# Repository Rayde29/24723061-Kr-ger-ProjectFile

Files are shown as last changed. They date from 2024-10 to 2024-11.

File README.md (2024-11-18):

# 24723061-Kruger-ProjectFile
Project File for Rayde Krüger-24723061- or Skripise Topic- Tip-thrust rotary wing aircraft
The file called Excel contains "Skripsie Budget" Which contains the budget and pin out for both boards used

Link to video:
https://1drv.ms/v/c/f0bb25edffddc46e/EVAi9ZLe4j9GsjdCYFR9vUkBoQ6bgEeh0lFj6d0QRGKrNw?e=6Zq3nG

Link to Code:
https://github.com/Rayde29/Skripsie_Code.git

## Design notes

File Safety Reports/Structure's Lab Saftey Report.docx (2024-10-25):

Mechatronics Lab Safety Report

Testing of a Tip-Thrust Rotary Aircraft

Date: | 23/09/2024
Student & SU nr: | Rayde Krüger 24723061
Student contact nr: | 063 694 9735
Supervisor: | Dr Andrew Gill
Lab engineer: | Mr Ferdi Zietsman
Head of safety: | Mr Cobus Zietsman

Emergency Contacts:

Contact: | Room nr. | Work nr. | Cell nr.
Mr F. Zietsman | 109 | - | 021 808 4954
Mr C. Zietsman | M212 | 021 808 4275 | -
Campus Security | - | 021 808 2333 | WhatsApp: 082 808 233
Fire Brigade | - | 021 808 8888 | -
Ambulance | - | 021 883 3444 | -

Signatures:

Student: (Rayde Krüger)
Supervisor: (Dr A. Gill)
Lab Engineer: (Mr CF. Zietsman)
Head of Safety: (C Zietsman)

Pressure vessels or pipes (check relevant box):

☒ No pressure vessels or pipes with pressure in excess of 50kPa are involved in this project.

☐ Pressure vessels or pipes in excess of 50kPa are involved – additional signature and report required (refer to Safety Report Guidelines on SUNLearn).

Hot work / working at heights / confined entry / excavation (check relevant box):

☒ No hot work / working heights / confined entry / excavation work involved in this project.

☐ Hot work / working heights / confined entry / excavation work (underline relevant work type(s)) involved in this project – additional signature and report required (refer to Safety Report Guidelines on SUNLearn).

Overview of Testing

Type of test and standard (if applicable):

Test type | Testing of tip-thrust rotary aircraft
Standard(s) | IEC 60950-1 / IEC 62368-1:

Equipment to be used:

Equipment type | Make & model | Measurement range (if applicable) | Resolution (if applicable)
40 A DC power supply | - | - | -
Oscilloscope | - | - | -
Soldering Iron | - | - | -
Load Cell 50KG | TAL220 Series | 0 to 50 kg | -
Load Cell Amplifier | HX711 | - | 24-bit

Detailed Experimental Procedure

The purpose of this section is to clearly communicate the purpose of equipment use and list the steps necessary to prepare the equipment for testing. This report will describe the testing of a tip-thrust rotary aircraft, and the risks associated with them. The purpose of the testing will be to determine the behaviour of the system’s rotor, the amount of thrust produced, and if directional thrust can be achieved.

Pitch control testing setup:

- Assemble the rotary wing aircraft
- Secure the rotary wing aircraft to the base
- Secure the rotor hub so it cannot rotate
- Ensure the correct voltage is being supplied by the power supply
- Connect the power supply to the hub
- Identify the emergency stop button (Power supply off switch)
- Ensure all the components have been correctly wired
- Ensure all wires, loose items or clothing are clear of the motors

Pitch control testing procedures:

- Switch on the power supply
- Ensure the hub is secure and there are no obstructions in its path in the event that it comes loose and rotates
- Calibrate the pitch sensor of the rotor
- Activate the tip-thrust motors on low-speed
- Slowly increase the thrust until the desired speed of the tip thrust motors, ensuring that the hub remains stationary
- Once the rotor is stable, set a target pitch for the PID controller to reach
- Change the target pitch multiple times to determine the response speed for the different pitch values.
- Record the results in an Excell spreadsheet
- Switch off the tip-thrust motors and repeat the experiment

Directional thrust testing setup:

- Assemble the rotary wing aircraft
- Secure the rotary wing aircraft to the base
- Ensure there are no obstructions in the rotor's path
- Ensure all components are securely attached to the aircraft
- Connect the load cells to the DAQ and ensure they are being received
- Calibrate the load cells using known weights
- Ensure the correct voltage is being supplied by the power supply
- Identify the emergency stop button (Power supply off switch)
- Ensure all the components have been correctly wired
- Connect the power supply to the hub
- Ensure all wires, loose items or clothing are clear of the motors

Directional thrust testing procedure:

- Switch on the power supply
- Calibrate the rotor pitch sensor
- Ensure that the rotor path is clear of any obstructions before switching on the tip-thrust motors on low-speed
- Set the target angular velocity of the rotor
- Wait until the angular velocity has become steady
- Record the response of the control system
- Record the data from the load cells
- Set directional flight mode
- Record the data from the load cells
- Repeat the experiment for different angular velocities and directions

Shut down procedure:

- Stop the software of the microcontroller and ensure all components are in a state to power down
- Turn off the power supply
- Wait until all components have stopped moving
- Remove the rotary wing aircraft from the base
- Disassemble components to fit into storage
- Remove the load cells
- Safely store components
- Clean up workstation

Warning Symbols

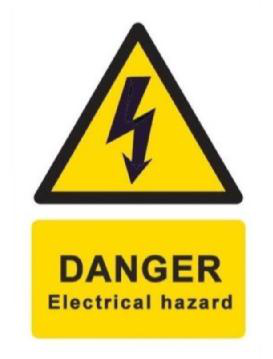
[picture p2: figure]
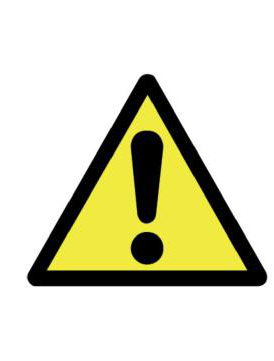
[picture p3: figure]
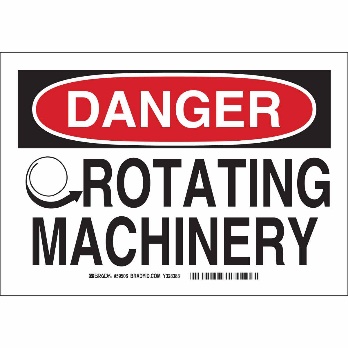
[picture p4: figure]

(a) Electrical hazard (b) General Warning (c) Rotating machinery warning

Figure 1: Applicable warning/hazard symbols

General Laboratory Safety

The following general laboratory safety instructions are applicable:

- No afterhours testing may be performed without the necessary permissions[^1].
- Full supervised training is required before testing may be undertaken. Permission to proceed with unsupervised testing should be signed off by the lab engineer.
- Closed shoes must be worn at all times.
- Emergency equipment must be located and easily accessible.
- Students may not work alone in the laboratory.
- Emergency exits must be known. The nearest exits applicable to the setup are provided in Appendix A of this document
- Loose clothing may not be worn. Loose hair must be tied up.
- Good housekeeping practices should be maintained during testing. The lab should be completely clean, including all equipment stored away, after testing. Refer to the General Housekeeping section for particulars regarding practices to be followed for this specific setup.
- No food or drink is permitted in the laboratory.
- Safety report must be visible and accessible during testing.
- No equipment or test may be left unattended.

Anticipated Interactions with Other Laboratory Users

Barriers between the rotary wing aircraft and other nearby projects to reduce the risk of components falling off and striking another student or their project.

General Housekeeping

- Keep workspace tidy while working
- Switch off power supplies after use
- Disassemble the rotor and place it in its storage
- Clean working surface, remove any debris and off cuttings
- Return all equipment to their storage
- Ensure the workstation is clear and clean
- Ensure no personal items are left behind

Fire Safety

The DC motors could potentially overheat. This can be avoided by ensuring the motors operate below the maximum operating voltage, ensuring that they do not overheat. Parts of the circuit could short and cause a fire. This hazard can be mitigated by using properly insulated wires and labelling the wires, so wires aren’t incorrectly connected and by having neat solders. In case of a fire, the evacuation plan can be seen in Appendix A. No earphones should be worn while working so fire alarms can be heard.

Activity Based Risk Assessment

Activity | Risk | Risk Type* (P/E) | Mitigating Steps | Classification of Risk Severity

GENERAL
Moving around the lab | Tripping or knocking over equipment | P | Be aware of the surrounding equipment and environment when walking in the lab | Acceptable risk
Power outages | Data loss and damage to equipment | E | Check the loadshedding schedule beforehand | Possible risk
Personal items | Theft of items | P | Don’t leave personal items unattended | Acceptable risk

TESTING PHASE
Installing electrical components | Electric shocks | P | Ensure the power is off when working with the components | Possible risk
| Shorting electrical components | E | Ensure all components are connected correctly before powering them | Acceptable risk
| Incorrect connections | E | Ensure components are connected according to the wiring diagram | Acceptable risk
Using hand tools | Injuries due to slippage | P | Ensure if a tool slips, no injuries can occur | Acceptable risk
Installing motors | Dropping motors | E | Handle motors with care | Acceptable risk
Assembling rotor | Pinching fingers | P | Ensure fingers are not caught in between components while assembling | Acceptable risk
Incorrect Calibration | Aircraft is uncontrollable | P/E | After calibrating the pitch, ensure the readings are correct | Acceptable risk
Loose wires or clothing caught in the motors | Getting items entangled by the motors | P/E | Don’t wear loose clothing and ensure any loose items are kept away from the motors | Acceptable risk
Rotor turning | Impact with the rotor | P/E | Ensure there are no obstructions with the rotors’ path | Possible risk
| Items detach from the rotor | P/E | Check that all items are securely attached to the rotor and hub | Possible risk
Rotor turning | Rotary aircraft tips over | P/E | Ensure the base is firmly secured | Possible risk
Load cell failure | Incorrect readings from the load cells | E | Calibrate the load cells before use | Acceptable risk
Testing motor | Motors overheat | E | Ensure the motors operate within the rated values | Acceptable risk
| Burns occur from motor overheating | P | Ensure the motors operate within the rated values | Acceptable risk
Testing software | Code not working as intended | P/E | Ensure the code is fully understood before it is uploaded | Acceptable risk
Backing up data | Data loss | E | Use a USB/ hard drive which is frequently updated. | Acceptable risk

*P – personal, E - equipment

Disciplinary Actions

Failure to comply with any of the aforementioned safety regulations or procedures will result in disciplinary action. Students will be issued an initial warning: after three warnings, the lab access is revoked for a month.

Appendix A: Emergency Evacuation Plans

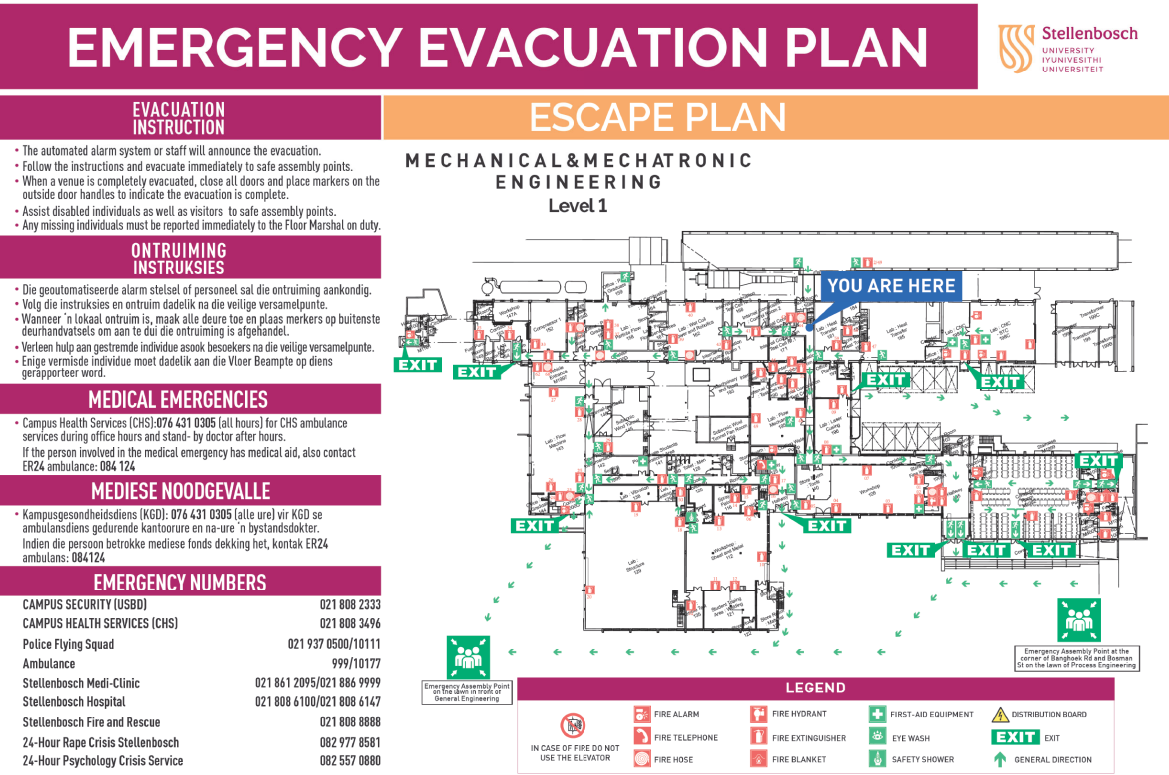
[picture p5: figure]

[^1] Written permission from supervisor and approved by the chief safety officer. Attach proof of this permission to this document and note here the times and conditions of the arrangement.

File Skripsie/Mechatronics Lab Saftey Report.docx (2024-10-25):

Mechatronics Lab Safety Report

Testing of Electronic Components and assembly of a Tip-Thrust Rotary Aircraft

Date: | 08/07/2024
Student & SU nr: | Rayde Krüger 24723061
Student contact nr: | 063 694 9735
Supervisor: | Dr Andrew Gill
Lab engineer: | Mr Kevin Neaves
Head of safety: | Mr Cobus Zietsman

Emergency Contacts:

Contact: | Room nr. | Work nr. | Cell nr.
Mr K. Neaves | 3001 | - | 021 808 4279
Mr C. Zietsman | M212 | 021 808 4275 | -
Campus Security | - | 021 808 2333 | WhatsApp: 082 808 233
Fire Brigade | - | 021 808 8888 | -
Ambulance | - | 021 883 3444 | -

Signatures:

Student: (Rayde Krüger)
Supervisor: (Dr A. Gill)
Lab Engineer: (Mr K. Neaves)
Head of Safety: (C Zietsman)

Pressure vessels or pipes (check relevant box):

☒ No pressure vessels or pipes with pressure in excess of 50kPa are involved in this project.

☐ Pressure vessels or pipes in excess of 50kPa are involved – additional signature and report required (refer to Safety Report Guidelines on SUNLearn).

Hot work / working at heights / confined entry / excavation (check relevant box):

☒ No hot work / working heights / confined entry / excavation work involved in this project.

☐ Hot work / working heights / confined entry / excavation work (underline relevant work type(s)) involved in this project – additional signature and report required (refer to Safety Report Guidelines on SUNLearn).

Overview of Testing

Type of test and standard (if applicable):

Test type | Testing electronic components and assembly of tip-thrust rotary aircraft
Standard(s) | IEC 60950-1 / IEC 62368-1:

Equipment to be used:

Equipment type | Make & model | Measurement range (if applicable) | Resolution (if applicable)
Power supply | - | - | -
Oscilloscope | - | - | -
Soldering Iron | - | - | -

Detailed Experimental Procedure

The purpose of this section is to clearly communicate the purpose of equipment use and list the steps necessary to prepare the equipment for testing. This report will describe the testing of the electronic components as well as the assembly of the tip-thrust rotary aircraft and the risks associated with them. The purpose of the testing will be to determine the behaviour of the electronics and to test the microcontroller’s programming to control these components. The tip-thrust aircraft will be assembled in the Mechatronics lab, but not tested and no propellers will be connected to the brushless motors during testing.

Electronics testing setup:

- Read through the electronic components datasheet and take note of the components' operating voltages
- Identify the emergency stop button (Power supply off switch)
- Ensure all wire connections are securely connected and no cables or components appear damaged.
- Label all wires to prevent incorrect connections
- Verify the power supply and the oscilloscope are functioning correctly

Testing procedure for electronics:

- Connect the electronic component being tested according to the wiring diagram
- Switch on the power supply and check the output voltage.
- Test the output signal from the microcontroller and the output of the electronic component being tested on the oscilloscope
- Run the microcontroller's program to be tested and observe how the components
- Change the program as needed and repeat

Assembly procedure for Tip-thrust Rotary Aircraft:

- Ensure all parts to be assembled are undamaged and function as intended.
- Assemble the parts as described by the CAD model.
- Install electronic components according to the design specifications
- Ensure all wiring is connected correctly and secured to prevent movement of the wiring.

Shut down procedure:

- Stop the software of the microcontroller and ensure all components are in a state to power down
- Turn off the power supply and oscilloscope
- Disassemble components to fit into storage
- Safely store components
- Clean up workstation

Warning Symbols


(a) Electrical hazard (b) General Warning

Figure 1: Applicable warning/hazard symbols

General Laboratory Safety

The following general laboratory safety instructions are applicable:

- No afterhours testing may be performed without the necessary permissions[^1].
- Full supervised training is required before testing may be undertaken. Permission to proceed with unsupervised testing should be signed off by the lab engineer.
- Closed shoes must be worn at all times.
- Emergency equipment must be located and easily accessible.
- Students may not work alone in the laboratory.
- Emergency exits must be known. The nearest exits applicable to the setup are provided in Appendix A of this document
- Loose clothing may not be worn. Loose hair must be tied up.
- Good housekeeping practices should be maintained during testing. The lab should be completely clean, including all equipment stored away, after testing. Refer to the General Housekeeping section for particulars regarding practices to be followed for this specific setup.
- No food or drink is permitted in the laboratory.
- Safety report must be visible and accessible during testing.
- No equipment or test may be left unattended.

Anticipated Interactions with other Laboratory Users

If possible, the student’s experimental setup will remain within the workspace with a space in between the nearest experiment.

General Housekeeping

- Keep workspace tidy while working
- Switch off power supplies after use
- Disassemble the rotor and place it in its storage
- Clean working surface, remove any debris and off cuttings
- Return all equipment to their storage
- Ensure the workstation is clear and clean
- Ensure no personal items are left behind

Fire Safety

The DC motors could potentially overheat. This can be avoided by ensuring the motors operate below the maximum operating voltage, ensuring that they do not overheat. Parts of the circuit could short and cause a fire. This hazard can be mitigated by using properly insulated wires and labelling the wires, so wires aren’t incorrectly connected and by having neat solders. In case of a fire, the evacuation plan can be seen in Appendix A. No earphones should be worn while working so fire alarms can be heard.

Activity Based Risk Assessment

Activity | Risk | Risk Type* (P/E) | Mitigating Steps | Classification of Risk Severity

GENERAL
Moving around the lab | Tripping or knocking over equipment | P | Be aware of the surrounding equipment and environment when walking in the lab | Acceptable risk
Power outages | Data loss and damage to equipment | E | Check the loadshedding schedule beforehand | Possible risk
Personal items | Theft of items | P | Don’t leave personal items unattended | Acceptable risk

ASSEMBLY PHASE
Soldering components | Burns from equipment and solder | P | Handle the equipment carefully | Acceptable risk
| Damage components | E | Ensure the soldering iron is not placed where it could damage the component | Acceptable risk
Installing electrical components | Electric shocks | P | Ensure the power is off when working with the components | Acceptable risk
| Shorting electrical components | E | Ensure all components are connected correctly before powering them | Acceptable risk
| Incorrect connections | E | Ensure components are connected according to the wiring diagram | Acceptable risk
Using hand tools | Injuries due to slippage | P | Ensure if a tool slips, no injuries can occur | Acceptable risk
Installing motors | Dropping motors | E | Handle motors with care | Acceptable risk
Assembling rotor | Pinching fingers | P | Ensure fingers are not caught in between components while assembling | Acceptable risk
| Cuts from burrs | P | Clean the edges of cut components | Acceptable risk

TESTING PHASE
Testing motor | Motors overheat | E | Ensure the motors operate within the rated values | Acceptable risk
| Burns occur from motor overheating | P | Ensure the motors operate within the rated values | Acceptable risk
Testing software | Code not working as intended | P/E | Ensure the code is fully understood before it is uploaded | Acceptable risk
Backing up data | Data loss | E | Use a USB/ hard drive which is frequently updated. | Acceptable risk

*P – personal, E - equipment

Disciplinary Actions

Failure to comply with any of the aforementioned safety regulations or procedures will result in disciplinary action. Students will be issued an initial warning: after three warnings, the lab access is revoked for a month.

Appendix A: Emergency Evacuation Plans

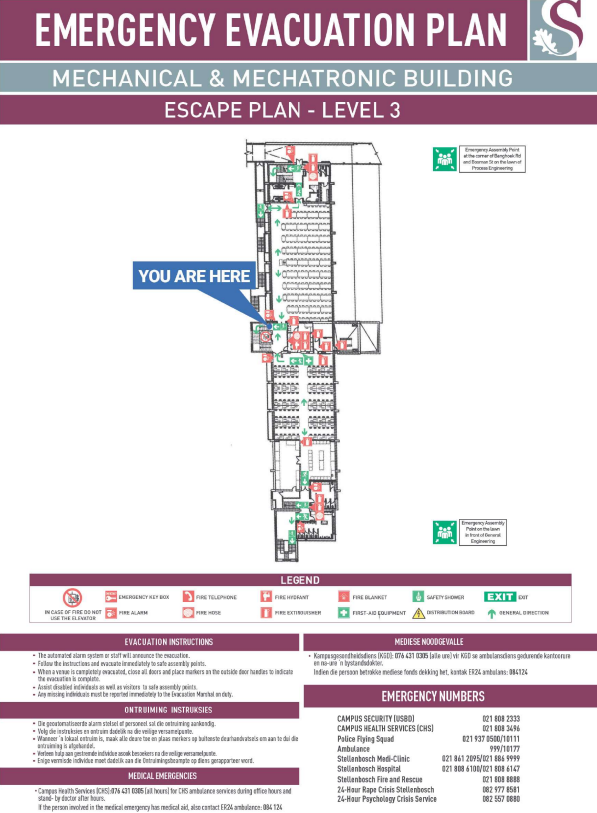
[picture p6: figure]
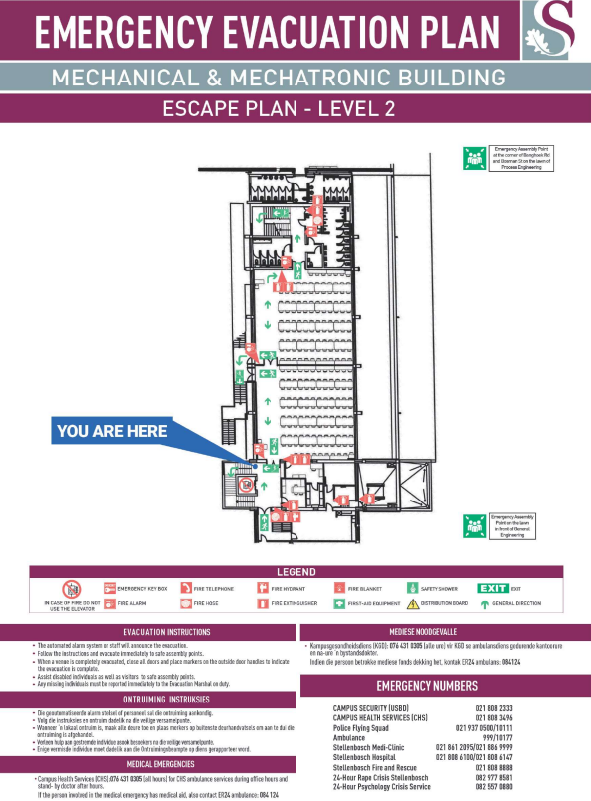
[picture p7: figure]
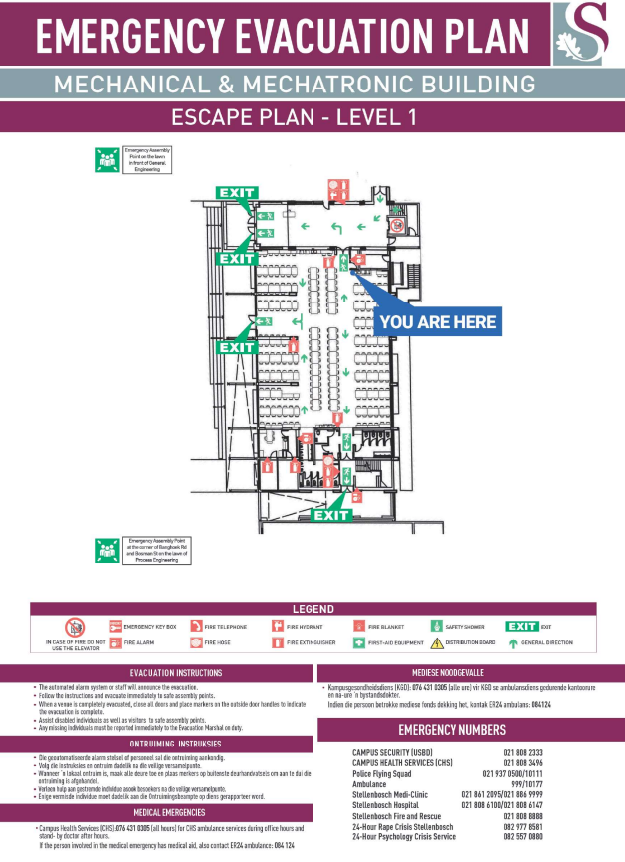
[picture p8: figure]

[^1] Written permission from supervisor and approved by the chief safety officer. Attach proof of this permission to this document and note here the times and conditions of the arrangement.

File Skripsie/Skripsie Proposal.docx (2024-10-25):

# Skripsie proposal: Tip-propelled rotary-wing aircraft

## Goal:

The goal of this project will be to design and build a rotary-wing aircraft which actuates its blades through the use of propulsion situated at the tip of the blades. The variation in propulsion should control translation in both the vertical and horizontal plane (the lift and rotor blade pitch). The aircraft should demonstrate that it is controllable and can sustain flight while being stable.

## Tentative Questions

### Can the rotary-wing aircraft be fully controlled using just the tip propulsion?

Investigate to determine if the direction of the aircraft be can controlled by adjusting the thrust generated from the tip propulsion or are external actuators and mechanisms, such as a swashplate, are required.

## Background

Traditional methods for actuating the blades consist of using a turboshaft engine to drive the rotor shaft, which rotates the blades. According to Newton's third law, the motor causes a torque on the fuselage from where the engine bevel gear connects to the rotor bevel gear and thus a tail rotor is required to compensate for this force. The tail rotor is mechanically linked to the main rotor so its rotational speed cannot change, instead to increase are decrease its force, the pitch of the blades is adjusted. Similarly, to move the helicopter in a certain direction the pitch of the blades at certain positions is adjusted using a swashplate, which would cause an increase in the pitch at one point and a decrease at the opposite point. This would create increased lift from the blade with the higher pitch and conversely, the decreased pitch would reduce lift. This creates a force upward force and a downward force located opposite to the upward force creating a moment about the fuselage. As seen with gyroscopic procession, this causes the force to act perpendicular to the applied force. Moving the helicopter in the direction of the force.

Traditional helicopters rely on the tail rotor to maintain control, if it malfunctions, it will cause the helicopter to become uncontrollable. The proposed idea to use tip propulsion to produce rotation has the benefit of eliminating the toque felt by the fuselage and thus eliminating the need for a tail rotor, with the added benefit of it being cheaper, lighter and reducing the need for high gearboxes and clutches. (Nenad Kolarević, 2020)

Research has shown most propulsion-tipped rotary aircraft make use of small jet engines placed at the tips of the blade. This was witnessed in the design of the Fairey Rotodyne. While the Rotodyne was a gyrodyne, meaning it made use of freely rotating rotor blades to produce lift, it had jet-tipped blades to allow for hovering and vertical take-off and landing. While this was intended to revolutionise air travel, the jet tips proved to be too loud for its intended purpose of inter-city travel (Mustard, 2019). Another option, which proved to be effective is demonstrated in the French helicopter the SO 1221S Djin, which made use of compressed air from a turbine-driven air compressor. (Heli archive, 2023).

As seen, this concept has been explored and has some benefits, yet is still fairly rare. Some of the disadvantages of this type of articulation are transmitting power to the rotating tips, increased noise, and the fact that there is added weight cantilevered at the end of the blade tips. These are a few of the challenges that need to be considered when creating the design for a propulsion-tipped rotary aircraft.

## Project Synopsis

### Propulsion

The first step required is a decision on the type of propulsion. These include jet engines, compressed air or by using electrical motors. It is believed that even at this time the possibility of jet engines can be ruled out for various reasons, leaving compressed air and electrical motors. Using the motors, a battery could be used to store potential energy, whereas a tank would be needed for compressed air. Controlling the speed can easily be done by increasing and decreasing the voltage to the electric motors, whereas for the compressed air, the output nozzle would need to increase and decrease in diameter, potentially with an iris mechanism and a servo motor. Lastly, the stored energy needs to be transmitted through the rotating blades, this can be achieved through a slip ring for the electric motors or using a swivel connector for the compressed air.

The only advantage of using the compressed air over the electric motors is that there wouldn’t need to be anything mounted at the tip of the wings, as it can be transmitted through tubing to the tips. While more research should be done into the matter, the electric motors have more precise control, most likely have a longer flight time and are less complicated. There is a high likelihood that this will be the chosen option moving forward.

### Designing and Controllability

Experiments need to be done to determine a method to adjust the pitch of the blade. Possible methods include the traditional use of a swashplate, actuators on each blade or by making a mechanism for which varying the individual speed of the tip propulsions adjusts the pitch. No CFD will be expected to be done.

Once the pitching mechanism has been decided on, the first prototype can be designed and created. This prototype will make use of a microcontroller and various sensors to ensure the aircraft can be controlled. A control system for this system will have to be made for this to make it possible to control the motion. Due to the complex nature and the desired control of this model, a state space controller would be the best choice, however, it may be difficult to derive an accurate model for the system and thus a PID controller might need to be used instead. The prototype will take in human input and not be autonomous.

### Testing

Once a control system has been implemented the prototype can be tested by securing it to four load cells (presumably in an ‘X’ configuration). From the load cells, it will be seen if thrust can be created such that the aircraft will go in the direction that has been instructed of it, thereby demonstrating the controllability of the prototype.

## Final remarks

The above illustrates the basic procedure that will be followed when designing and building the tip-propelled rotary-wing aircraft. Whilst care has been taken, it is anticipated that additional problems will be encountered during the course of this work, the overcoming of which will be an exciting challenge.

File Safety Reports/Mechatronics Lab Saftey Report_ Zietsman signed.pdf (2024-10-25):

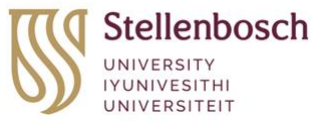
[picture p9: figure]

# Mechatronics Lab Safety Report

### Testing of Electronic Components and assembly of a Tip-Thrust Rotary Aircraft

Date: | 08/07/2024
Student & SU nr: | Rayde Krüger 24723061
Student contact nr: | 063 694 9735
Supervisor: | Dr Andrew Gill
Lab engineer: | Mr Kevin Neaves
Head of safety: | Mr Cobus Zietsman

Emergency Contacts:

Contact: | Room nr. | Work nr. | Cell nr.
Mr K. Neaves | 3001 | - | 021 808 4279
Mr C. Zietsman | M212 | 021 808 4275 | -
Campus Security | - | 021 808 2333 | WhatsApp: 082 808 233
Fire Brigade | - | 021 808 8888 | -
Ambulance | - | 021 883 3444 | -

Signatures:

Student: (Rayde Krüger) | motors.

Supervisor: (Dr A. Gill)

Lab Engineer: (Mr K. Neaves) | 12/8/2024

Head of Safety: (C Zietsman)

Pressure vessels or pipes (check relevant box):
☒ | No pressure vessels or pipes with pressure in excess of 50kPa are involved in this project.
☐ | Pressure vessels or pipes in excess of 50kPa are involved – additional signature and report
required (refer to Safety Report Guidelines on SUNLearn).

Hot work / working at heights / confined entry / excavation (check relevant box):
☒ | No hot work / working heights / confined entry / excavation work involved in this project.
☐ | Hot work / working heights / confined entry / excavation work (underline relevant work
type(s)) involved in this project – additional signature and report required (refer to Safety Report Guidelines on SUNLearn).

## Ensure no wires, loose items of clothing hair etc. is clear of the

### Overview of Testing

Type of test and standard (if applicable):

Test type | Testing electronic components and assembly of tip-thrust rotary aircraft
Standard(s) | IEC 60950-1 / IEC 62368-1:

Equipment to be used:

Equipment type | Make & model | Measurement range (if applicable) | Resolution (if applicable)
Power supply | - | - | -
Oscilloscope | - | - | -
Soldering Iron | - | - | -

### Detailed Experimental Procedure

The purpose of this section is to clearly communicate the purpose of equipment use and list the steps necessary to prepare the equipment for testing. This report will describe the testing of the electronic components as well as the assembly of the tip-thrust rotary aircraft and the risks associated with them. The purpose of the testing will be to determine the behaviour of the electronics and to test the microcontroller’s programming to control these components. The tip-thrust aircraft will be assembled in the Mechatronics lab, but not tested and no propellers will be connected to the brushless motors during testing.
Electronics testing setup:
- Read through the electronic components datasheet and take note of the components' operating voltages
- Identify the emergency stop button (Power supply off switch)
- Ensure all wire connections are securely connected and no cables or components appear damaged.
- Label all wires to prevent incorrect connections
- Verify the power supply and the oscilloscope are functioning correctly
Testing procedure for electronics:
- Connect the electronic component being tested according to the wiring diagram
- Switch on the power supply and check the output voltage.
- Test the output signal from the microcontroller and the output of the electronic component being tested on the oscilloscope
- Run the microcontroller's program to be tested and observe how the components
- Change the program as needed and repeat

Assembly procedure for Tip-thrust Rotary Aircraft:

- Ensure all parts to be assembled are undamaged and function as intended.
- Assemble the parts as described by the CAD model.
- Install electronic components according to the design specifications
- Ensure all wiring is connected correctly and secured to prevent movement of the wiring.

Shut down procedure:

- Stop the software of the microcontroller and ensure all components are in a state to power down
- Turn off the power supply and oscilloscope
- Disassemble components to fit into storage
- Safely store components
- Clean up workstation

### Warning Symbols

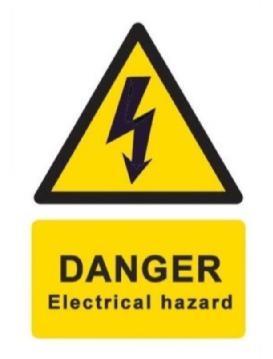
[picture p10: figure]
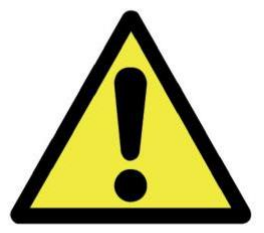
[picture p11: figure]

(a) Electrical hazard | (b) General Warning

Figure 1: Applicable warning/hazard symbols

### General Laboratory Safety

The following general laboratory safety instructions are applicable:

- No afterhours testing may be performed without the necessary permissions¹
- Full supervised training is required before testing may be undertaken. Permission to proceed with unsupervised testing should be signed off by the lab engineer.
- Closed shoes must be worn at all times.
- Emergency equipment must be located and easily accessible.
- Students may not work alone in the laboratory.
- Emergency exits must be known. The nearest exits applicable to the setup are provided in Appendix A of this document
- Loose clothing may not be worn. Loose hair must be tied up.
- Good housekeeping practices should be maintained during testing. The lab should be completely clean, including all equipment stored away, after testing. Refer to the General Housekeeping section for particulars regarding practices to be followed for this specific setup.
- No food or drink is permitted in the laboratory.

1 Written permission from supervisor and approved by the chief safety officer. Attach proof of this permission to this document and note here the times and conditions of the arrangement.

- Safety report must be visible and accessible during testing.
- No equipment or test may be left unattended.

### Anticipated Interactions with other Laboratory Users

If possible, the student’s experimental setup will remain within the workspace with a space in between the nearest experiment.

### General Housekeeping

- Keep workspace tidy while working
- Switch off power supplies after use
- Disassemble the rotor and place it in its storage
- Clean working surface, remove any debris and off cuttings
- Return all equipment to their storage
- Ensure the workstation is clear and clean
- Ensure no personal items are left behind

### Fire Safety

The DC motors could potentially overheat. This can be avoided by ensuring the motors operate below the maximum operating voltage, ensuring that they do not overheat. Parts of the circuit could short and cause a fire. This hazard can be mitigated by using properly insulated wires and labelling the wires, so wires aren’t incorrectly connected and by having neat solders. In case of a fire, the evacuation plan can be seen in Appendix A. No earphones should be worn while working so fire alarms can be heard.

### Activity Based Risk Assessment

Activity | Risk | Risk Type* (P/E)
Mitigating Steps | Classification of Risk
Severity

GENERAL
Moving around the lab | Tripping or knocking over equipment | P | Be aware of the surrounding equipment and environment when walking in the lab | Acceptable risk
Power outages | Data loss and damage to equipment | E | Check the loadshedding schedule beforehand | Possible risk
Personal items | Theft of items | P | Don’t leave personal items unattended | Acceptable risk

ASSEMBLY PHASE
Soldering components | Burns from equipment and solder | P | Handle the equipment carefully | Acceptable risk
| Damage components | E | Ensure the soldering iron is not placed where it | Acceptable risk

| | | could damage the component
Installing electrical components | Electric shocks | P | Ensure the power is off when working with the components | Acceptable risk
| Shorting electrical components | E | Ensure all components are connected correctly before powering them | Acceptable risk
| Incorrect connections | E | Ensure components are connected according to the wiring diagram | Acceptable risk
Using hand tools | Injuries due to slippage | P | Ensure if a tool slips, no injuries can occur | Acceptable risk
Installing motors | Dropping motors | E | Handle motors with care | Acceptable risk
Assembling rotor | Pinching fingers | P | Ensure fingers are not caught in between components while assembling | Acceptable risk
| Cuts from burrs | P | Clean the edges of cut components | Acceptable risk

TESTING PHASE
Testing motor | Motors overheat | E | Ensure the motors operate within the rated values | Acceptable risk
| Burns occur from motor overheating | P | Ensure the motors operate within the rated values | Acceptable risk
Testing software | Code not working as intended | P/E | Ensure the code is fully understood before it is uploaded | Acceptable risk
Backing up data | Data loss | E | Use a USB/ hard drive which is frequently updated. | Acceptable risk

*P – personal, E - equipment

### Disciplinary Actions

Failure to comply with any of the aforementioned safety regulations or procedures will result in disciplinary action. Students will be issued an initial warning: after three warnings, the lab access is revoked for a month.

### Appendix A: Emergency Evacuation Plans

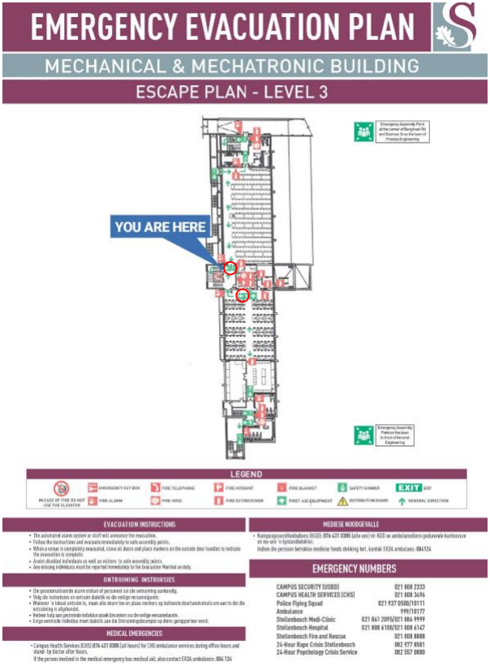
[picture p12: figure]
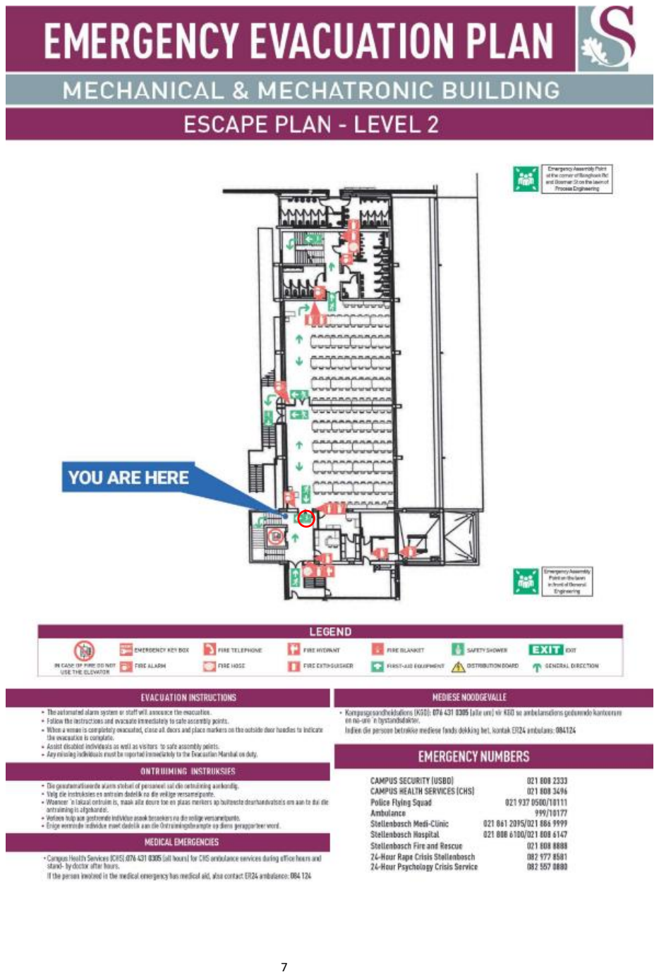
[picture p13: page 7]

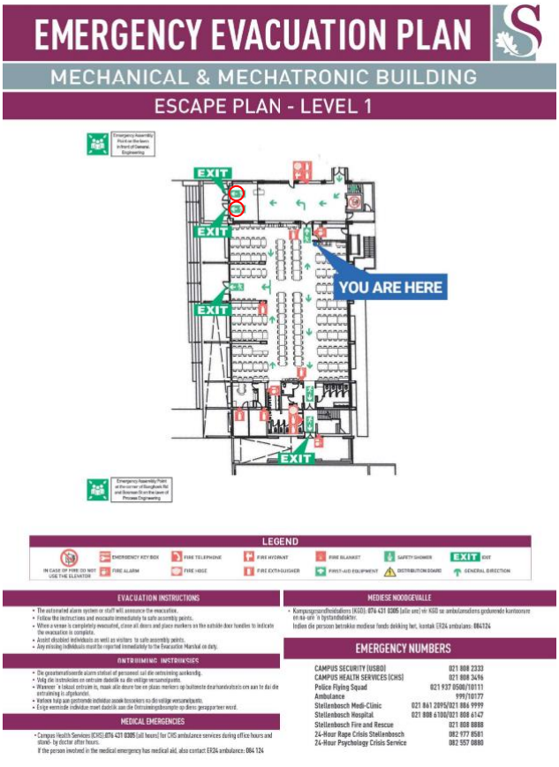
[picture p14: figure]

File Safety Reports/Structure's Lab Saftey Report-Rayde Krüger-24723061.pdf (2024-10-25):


# Mechatronics Lab Safety Report

### Testing of a Tip-Thrust Rotary Aircraft

Date: | 23/09/2024
Student & SU nr: | Rayde Krüger 24723061
Student contact nr: | 063 694 9735
Supervisor: | Dr Andrew Gill
Lab engineer: | Mr Ferdi Zietsman
Head of safety: | Mr Cobus Zietsman

Emergency Contacts:

Contact: | Room nr. | Work nr. | Cell nr.
Mr CF. Zietsman | 109 | - | 021 808 4954
Mr C. Zietsman | M212 | 021 808 4275 | -
Campus Security | - | 021 808 2333 | WhatsApp: 082 808 233
Fire Brigade | - | 021 808 8888 | -
Ambulance | - | 021 883 3444 | -

Signatures:

Student: (Rayde Krüger)

Supervisor: (Dr A. Gill)

Lab Engineer: (Mr CF. Zietsman)

Head of Safety: (C Zietsman)

Pressure vessels or pipes (check relevant box):
☒ | No pressure vessels or pipes with pressure in excess of 50kPa are involved in this project.
☐ | Pressure vessels or pipes in excess of 50kPa are involved – additional signature and report
required (refer to Safety Report Guidelines on SUNLearn).

Hot work / working at heights / confined entry / excavation (check relevant box):
☒ | No hot work / working heights / confined entry / excavation work involved in this project.
☐ | Hot work / working heights / confined entry / excavation work (underline relevant work
type(s)) involved in this project – additional signature and report required (refer to Safety Report Guidelines on SUNLearn).

### Overview of Testing

Type of test and standard (if applicable):

Test type | Testing of tip-thrust rotary aircraft
Standard(s) | IEC 60950-1 / IEC 62368-1:

Equipment to be used:

Equipment type | Make & model | Measurement range (if applicable) | Resolution (if applicable)
40 A DC power supply | - | - -
Oscilloscope | - | - | -
Soldering Iron | - | - | -
Load Cell 50KG | TAL220 Series | 0 to 50 kg | -
Load Cell Amplifier | HX711 | - | 24-bit

### Detailed Experimental Procedure

The purpose of this section is to clearly communicate the purpose of equipment use and list the steps necessary to prepare the equipment for testing. This report will describe the testing of a tip-thrust rotary aircraft, and the risks associated with them. The purpose of the testing will be to determine the behaviour of the system’s rotor, the amount of thrust produced, and if directional thrust can be achieved.

Pitch control testing setup:
- Assemble the rotary wing aircraft
- Secure the rotary wing aircraft to the base
- Secure the rotor hub so it cannot rotate
- Ensure the correct voltage is being supplied by the power supply
- Connect the power supply to the hub
- Identify the emergency stop button (Power supply off switch)
- Ensure all the components have been correctly wired
- Ensure all wires, loose items or clothing are clear of the motors

Pitch control testing procedures:
- Switch on the power supply
- Ensure the hub is secure and there are no obstructions in its path in the event that it comes loose and rotates
- Calibrate the pitch sensor of the rotor
- Activate the tip-thrust motors on low-speed
- Slowly increase the thrust until the desired speed of the tip thrust motors, ensuring that the hub remains stationary
- Once the rotor is stable, set a target pitch for the PID controller to reach
- Change the target pitch multiple times to determine the response speed for the different pitch values.
- Record the results in an Excell spreadsheet
- Switch off the tip-thrust motors and repeat the experiment

Directional thrust testing setup:
- Assemble the rotary wing aircraft
- Secure the rotary wing aircraft to the base
- Ensure there are no obstructions in the rotor's path
- Ensure all components are securely attached to the aircraft
- Connect the load cells to the DAQ and ensure they are being received
- Calibrate the load cells using known weights
- Ensure the correct voltage is being supplied by the power supply
- Identify the emergency stop button (Power supply off switch)
- Ensure all the components have been correctly wired
- Connect the power supply to the hub
- Ensure all wires, loose items or clothing are clear of the motors

Directional thrust testing procedure:
- Switch on the power supply
- Calibrate the rotor pitch sensor
- Ensure that the rotor path is clear of any obstructions before switching on the tip-thrust motors on low-speed
- Set the target angular velocity of the rotor
- Wait until the angular velocity has become steady
- Record the response of the control system
- Record the data from the load cells
- Set directional flight mode
- Record the data from the load cells
- Repeat the experiment for different angular velocities and directions

Shut down procedure:

- Stop the software of the microcontroller and ensure all components are in a state to power down
- Turn off the power supply
- Wait until all components have stopped moving
- Remove the rotary wing aircraft from the base
- Disassemble components to fit into storage
- Remove the load cells
- Safely store components
- Clean up workstation

### Warning Symbols

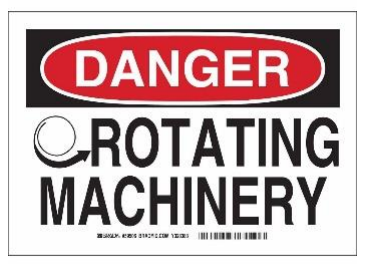
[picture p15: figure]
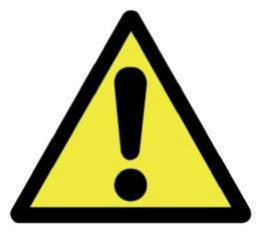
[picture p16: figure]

(a) Electrical hazard | (b) General Warning | (c) Rotating machinery warning

Figure 1: Applicable warning/hazard symbols

### General Laboratory Safety

The following general laboratory safety instructions are applicable:

- No afterhours testing may be performed without the necessary permissions¹
- Full supervised training is required before testing may be undertaken. Permission to proceed with unsupervised testing should be signed off by the lab engineer.
- Closed shoes must be worn at all times.
- Emergency equipment must be located and easily accessible.
- Students may not work alone in the laboratory.
- Emergency exits must be known. The nearest exits applicable to the setup are provided in Appendix A of this document
- Loose clothing may not be worn. Loose hair must be tied up.
- Good housekeeping practices should be maintained during testing. The lab should be completely clean, including all equipment stored away, after testing. Refer to the General Housekeeping section for particulars regarding practices to be followed for this specific setup.
- No food or drink is permitted in the laboratory.
- Safety report must be visible and accessible during testing.
- No equipment or test may be left unattended.

### Anticipated Interactions with Other Laboratory Users

Barriers between the rotary wing aircraft and other nearby projects to reduce the risk of components falling off and striking another student or their project.

### General Housekeeping

- Keep workspace tidy while working
- Switch off power supplies after use
- Disassemble the rotor and place it in its storage
- Clean working surface, remove any debris and off cuttings
- Return all equipment to their storage
- Ensure the workstation is clear and clean
- Ensure no personal items are left behind

### Fire Safety

1 Written permission from supervisor and approved by the chief safety officer. Attach proof of this permission to this document and note here the times and conditions of the arrangement.

The DC motors could potentially overheat. This can be avoided by ensuring the motors operate below the maximum operating voltage, ensuring that they do not overheat. Parts of the circuit could short and cause a fire. This hazard can be mitigated by using properly insulated wires and labelling the wires, so wires aren’t incorrectly connected and by having neat solders. In case of a fire, the evacuation plan can be seen in Appendix A. No earphones should be worn while working so fire alarms can be heard.

### Activity Based Risk Assessment

Activity | Risk | Risk Type* (P/E)
Mitigating Steps | Classification of Risk
Severity

GENERAL
Moving around the lab | Tripping or knocking over equipment | P | Be aware of the surrounding equipment and environment when walking in the lab | Acceptable risk
Power outages | Data loss and damage to equipment | E | Check the loadshedding schedule beforehand | Possible risk
Personal items | Theft of items | P | Don’t leave personal items unattended | Acceptable risk

TESTING PHASE
Installing electrical components | Electric shocks | P | Ensure the power is off when working with the components | Possible risk
| Shorting electrical components | E | Ensure all components are connected correctly before powering them | Acceptable risk
| Incorrect connections | E | Ensure components are connected according to the wiring diagram | Acceptable risk
Using hand tools | Injuries due to slippage | P | Ensure if a tool slips, no injuries can occur | Acceptable risk
Installing motors | Dropping motors | E | Handle motors with care | Acceptable risk
Assembling rotor | Pinching fingers | P | Ensure fingers are not caught in between components while assembling | Acceptable risk
Incorrect Calibration | Aircraft is uncontrollable | P/E | After calibrating the pitch, ensure the readings are correct | Acceptable risk
Loose wires or clothing caught in the motors | Getting items entangled by the motors | P/E | Don’t wear loose clothing and ensure any loose items are kept away from the motors | Acceptable risk
Rotor turning | Impact with the rotor | P/E | Ensure there are no obstructions with the rotors’ path | Possible risk
| Items detach from the rotor | P/E | Check that all items are securely attached to the rotor and hub | Possible risk

Rotor turning | Rotary aircraft tips over | P/E | Ensure the base is firmly secured | Possible risk
Load cell failure | Incorrect readings from the load cells | E | Calibrate the load cells before use | Acceptable risk
Testing motor | Motors overheat | E | Ensure the motors operate within the rated values | Acceptable risk
| Burns occur from motor overheating | P | Ensure the motors operate within the rated values | Acceptable risk
Testing software | Code not working as intended | P/E | Ensure the code is fully understood before it is uploaded | Acceptable risk
Backing up data | Data loss | E | Use a USB/ hard drive which is frequently updated. | Acceptable risk

*P – personal, E - equipment

### Disciplinary Actions

Failure to comply with any of the aforementioned safety regulations or procedures will result in disciplinary action. Students will be issued an initial warning: after three warnings, the lab access is revoked for a month.

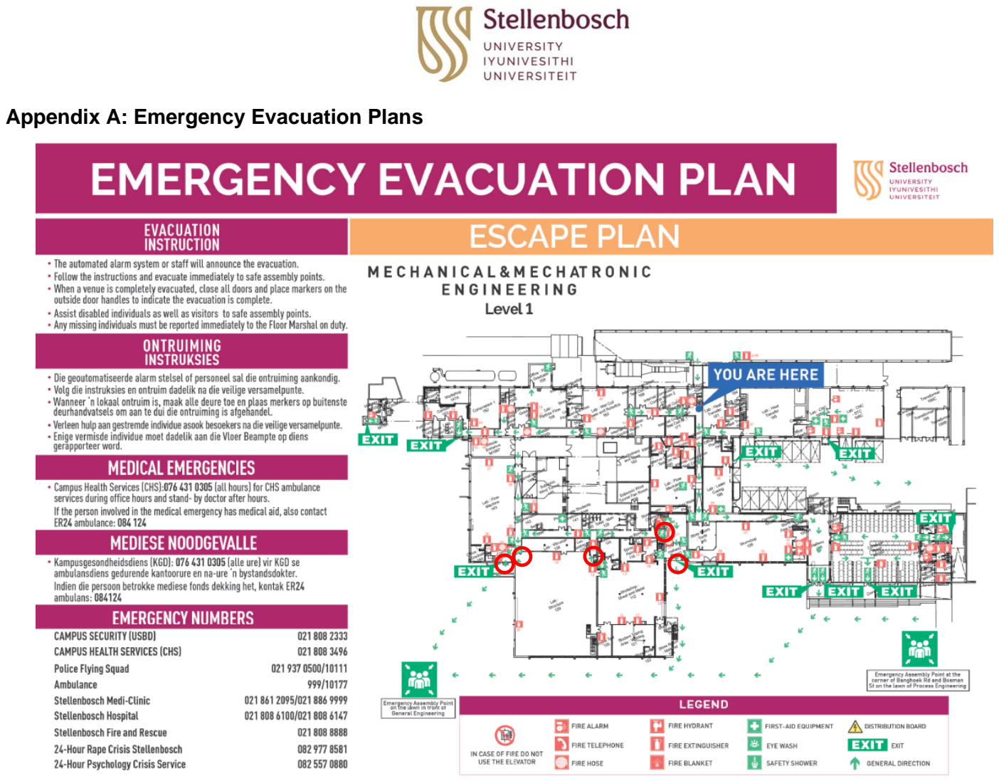
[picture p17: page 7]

### Appendix A: Emergency Evacuation Plans

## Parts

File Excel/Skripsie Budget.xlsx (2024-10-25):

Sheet: Full Budget
Item | Supplier | Price per unit | Quantity | Unit | Shipping | Category | Status | Total | Website | a
HKD NRF24L01+ TRANSCEIVER MODULE | Communica | R 29.00 | 2 | items | R 99.87 | Electronics | Received | R 157.88 |  |  | Not ordered
30a Electronic Speed Control Brushless | Takealot | R 230.00 | 4 | items | R 0.00 | Electroncis | Received | R 920.00 |  | s | Quote sent
Flash 1303.5 5500kv Brushless Motor | FPV Fanatics | R 285.00 | 4 | items | R 80.00 | Electroncis | Received | R 1220.00 |  | s | Ordered | 757
LOCK NUT 20X32X6MM M20X1.0 THREAD BTC | BMG | R 24.92 | 1 | items | R 80.00 | Mechanical | Received | R 104.92 | https://bmgworld.net/bmg/en/ZAR/All-Categories/Bearings/Accessories/Lock-Nuts/KM-04/p/KM%2004 | s | Received
BM0805FB-ISB (Bushing) | Bearings Online SA | R 23.00 | 4 | items | R 80.00 | Mechanical | Received | R 172.00 | https://bearingsonlinesa.co.za/shop/bm-0805-fb-8-x-10-x-5-isb/ | s
51104-ISB Thrust bearing | Bearings Online SA | R 95.00 | 2 | items | R 0.00 | Mechanical | Received | R 190.00 | https://bearingsonlinesa.co.za/shop/51104-20-x-35-x-10-isb/ | s
HQ Durable Prop 2.9X2.9X4 Grey | Flying Robot | R 45.00 | 1 | set | R 80.00 | Mechanical | Received | R 125.00 | https://flyingrobot.co/products/hq-durable-prop-2-9x2-9x4-grey-2cw-2ccw-poly-carbonate | s
 |  |  |  |  |  |  | Received
Hall effect | Micro Robotics | R 13.80 | 1 | packet (4) | R 0.00 | Electronics | Received | R 13.80 |  | s
Power Supply | Takealot | R 349.00 | 1 | items | R 0.00 | Electronics | Received | R 349.00
Slip Ring 4 Wire 20A Diameter 22mm | Micro Robotics | R 752.00 | 1 | items | R 0.00 | Electronics | Received | R 752.00
Magnets | Takealot | R 170.00 | 1 |  | R 0.00 | Mechanical | Received | R 170.00 |  | s
Black Bill | Micro Robotics | R 110.00 | 1 |  |  | Electronics | Received | R 110.00 |  | s
LEDS | Micro Robotics | R 25.00 | 1 | PACKET (25) |  | Electronics | Received | R 25.00
Wiring | Micro Robotics | R 33.00 | 2 | m | R 0.00 | Electronics | Received | R 66.00
Batterty Connectors | Micro Robotics | R 51.00 | 2 | items | R 0.00 | Electronics | Received | R 102.00
Regulators | Micro Robotics | R 19.00 | 1 | Packet | R 0.00 | Electronics | Received | R 19.00
3 pin connectors | Micro Robotics | R 34.00 | 4 | items | R 0.00 | Electronics | Received | R 136.00
 |  |  |  |  |  |  | Received | R 0.00
3D Printing |  | R 757.00 | 1 | 3D Prints | R 0.00 | Mechanical | Received | R 757.00 |  | s
Workshop |  | R 10.00 | 1 | Parts | R 0.00 | Mechanical | Received | R 10.00 |  | s
 |  |  |  |  |  |  | Received | R 0.00 |  | s
Total: |  |  |  |  | R 179.87 |  |  | R 5399.60
Predicted total: |  |  |  |  |  |  |  | R 5399.60

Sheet: Pin Out
Port | Pin | I/O Function | USART | ADC | PWM | SPI | TIM | FSMC | Other | Avliable | Function
PA | 0 | Digital I/O | None | ADC1_IN0 | None | None | TIM2_CH1_ETR | None | WKUP, RTC_TAMP1 | No | Rotor Pitch 1 | 12 V
PA | 1 | Digital I/O | None | ADC1_IN1 | None | None | TIM2_CH2, TIM5_CH2 | None | WKUP2, RTC_TAMP2 | No | Rotor Pitch 2 | 5 V
PA | 2 | Digital I/O | USART2_TX | ADC1_IN2 | TIM2_CH3 | None | TIM5_CH3 | None | ETH_MDIO | Yes |  | 3.3V
PA | 3 | Digital I/O | USART2_RX | ADC1_IN3 | TIM2_CH4 | None | TIM5_CH4 | None | ETH_MII_COL | No | SPI 1 Chip Enable | Data
PA | 4 | Digital I/O | None | ADC1_IN4 | None | SPI1_NSS | TIM5_CH1 | None | DAC_OUT1 | No | SP1 Chip Select 2 | Input/Output
PA | 5 | Digital I/O | None | ADC1_IN5 | None | SPI1_SCK | TIM5_CH2 | None | DAC_OUT2 | No | SPI 1 SCK | analogue/sensors
PA | 6 | Digital I/O | None | ADC1_IN6 | TIM3_CH1 | SPI1_MISO | TIM13_CH1 | None | ETH_MII_RX_CLK | No | SPI 1 MISO
PA | 7 | Digital I/O | None | ADC1_IN7 | TIM3_CH2 | SPI1_MOSI | TIM14_CH1 | None | ETH_MII_RX_DV | No | SPI 1 MOSI
PA | 8 | Digital I/O | None | None | TIM1_CH1 | None | TIM1_CH1N | None | MCO1 | Yes
PA | 9 | Digital I/O | USART1_TX | None | TIM1_CH2 | None | TIM1_CH2N | None | None | Yes
PA | 10 | Digital I/O | USART1_RX | None | TIM1_CH3 | None | TIM1_CH3N | None | None | Yes
PA | 11 | Digital I/O | USART1_CTS | None | None | None | TIM1_CH4 | None | OTG_FS_DM | Yes
PA | 12 | Digital I/O | USART1_RTS | None | None | None | TIM1_ETR | None | OTG_FS_DP | Yes
PA | 13 | Digital I/O | None | None | None | None | None | None | SWDIO | Yes
PA | 14 | Digital I/O | None | None | None | None | None | None | SWCLK | Yes
PA | 15 | Digital I/O | USART3_TX | None | None | SPI3_NSS | TIM2_CH1_ETR | None | JTDI | Yes
PB | 0 | Digital I/O | None | ADC1_IN8 | TIM3_CH3 | None | TIM8_CH2N | None | None | No | Tim3_ch 3 - PWM- Top Motor, Rotor 2
PB | 1 | Digital I/O | None | ADC1_IN9 | TIM3_CH4 | None | TIM8_CH3N | None | None | No | Tim3_ch 4 - PWM- Bottom Motor, Rotor 2
PB | 2 | Digital I/O | None | None | None | None | TIM2_CH4, TIM4_CH1 | None | Boot1 | Yes
PB | 3 | Digital I/O | USART2_CK | None | None | SPI1_SCK | TIM2_CH2, TIM5_CH2 | None | JTDO/TRACESWO | No | Green LED for Warning
PB | 4 | Digital I/O | USART3_CTS | None | None | SPI1_MISO | TIM3_CH1 | None | JTRST | No | Red LED for warning
PB | 5 | Digital I/O | USART3_RTS | None | None | SPI1_MOSI | TIM3_CH2 | None | I2C1_SMBA | No | Tim3_ch 2 - PWM- Bottom Motor, Rotor 1
PB | 6 | Digital I/O | USART1_TX | None | TIM4_CH1 | None | TIM16_CH1 | None | I2C1_SCL | Yes
PB | 7 | Digital I/O | USART1_RX | None | TIM4_CH2 | None | TIM17_CH1 | None | I2C1_SDA | Yes
PB | 8 | Digital I/O | USART1_CK | None | TIM4_CH3 | None | TIM16_CH1N | FSMC_D4 | I2C1_SCL | Yes
PB | 9 | Digital I/O | USART1_TX | None | TIM4_CH4 | None | TIM17_CH1N | FSMC_D5 | I2C1_SDA | Yes
PB | 10 | Digital I/O | USART3_TX | None | None | None | TIM2_CH3, TIM5_CH3 | None | I2C2_SCL | Yes
PB | 11 | Digital I/O | USART3_RX | None | None | None | TIM2_CH4, TIM5_CH4 | None | I2C2_SDA | Yes
PB | 12 | Digital I/O | USART3_CK | None | None | SPI2_NSS | None | FSMC_D13 | None | Yes
PB | 13 | Digital I/O | None | None | None | SPI2_SCK | TIM1_CH1N | FSMC_D14 | None | Yes
PB | 14 | Digital I/O | None | None | None | SPI2_MISO | TIM1_CH2N | FSMC_D15 | None | Yes
PB | 15 | Digital I/O | USART3_CTS | None | None | SPI2_MOSI | TIM1_CH3N | None | None | Yes
PC | 0 | Digital I/O | None | ADC1_IN10 | None | None | TIM8_CH1, TIM3_CH1 | None | None | No | WAS ACTING WERID
PC | 1 | Digital I/O | None | ADC1_IN11 | None | None | TIM8_CH2, TIM3_CH2 | None | ETH_MDC | No | Position Hall Effect Sensor
PC | 2 | Digital I/O | None | ADC1_IN12 | None | None | TIM8_CH3, TIM3_CH3 | None | ETH_MII_TXD2 | No | Revolution Hall Effect Sensor
PC | 3 | Digital I/O | None | ADC1_IN13 | None | None | TIM8_CH4, TIM3_CH4 | None | ETH_MII_TX_CLK | Yes
PC | 4 | Digital I/O | None | ADC1_IN14 | None | None | None | None | ETH_MII_RXD0, ETH_MII_RXD0 | Yes
PC | 5 | Digital I/O | None | ADC1_IN15 | None | None | None | None | ETH_MII_RXD1 | Yes
PC | 6 | Digital I/O | USART6_TX | None | TIM3_CH1 | None | TIM8_CH1 | None | None | No | Tim3_ch 1 - PWM Top Motor, Rotor 1
PC | 7 | Digital I/O | USART6_RX | None | TIM3_CH2 | None | TIM8_CH2 | None | None | Yes
PC | 8 | Digital I/O | USART6_CK | None | TIM3_CH3 | None | TIM8_CH3 | None | None | Yes
PC | 9 | Digital I/O | USART6_CTS | None | TIM3_CH4 | None | TIM8_CH4 | None | None | Yes
PC | 10 | Digital I/O | USART3_TX | None | None | SPI3_SCK | TIM8_CH3 | None | None | Yes
PC | 11 | Digital I/O | USART3_RX | None | None | SPI3_MISO | TIM8_CH4 | None | None | Yes
PC | 12 | Digital I/O | USART3_CK | None | None | SPI3_MOSI | TIM8_CH4N | None | None | Yes
PC | 13 | Digital I/O | None | None | None | None | None | None | RTC_TAMP1, TAMP2 | Yes
PC | 14 | Digital I/O | None | None | None | None | None | None | OSC32_IN | Yes
PC | 15 | Digital I/O | None | None | None | None | None | None | OSC32_OUT | Yes
PD | 0 | Digital I/O | None | None | None | None | TIM4_CH1 | FSMC_D2 | None | Yes
PD | 1 | Digital I/O | None | None | None | None | TIM4_CH2 | FSMC_D3 | None | Yes
PD | 2 | Digital I/O | None | None | None | None | TIM3_ETR | FSMC_D4 | None | Yes
PD | 3 | Digital I/O | None | None | None | None | TIM2_CH1_ETR | FSMC_D5 | None | Yes
PD | 4 | Digital I/O | None | None | None | None | TIM2_CH2 | FSMC_D6 | None | Yes
PD | 5 | Digital I/O | None | None | None | None | TIM2_CH3 | FSMC_D7 | None | Yes
PD | 6 | Digital I/O | None | None | None | None | TIM2_CH4 | FSMC_D8 | None | Yes
PD | 7 | Digital I/O | None | None | None | None | TIM2_ETR | FSMC_D9 | None | Yes
PD | 8 | Digital I/O | None | None | None | None | TIM3_CH1 | FSMC_D10 | None | Yes
PD | 9 | Digital I/O | None | None | None | None | TIM3_CH2 | FSMC_D11 | None | Yes
PD | 10 | Digital I/O | None | None | None | None | TIM3_CH3 | FSMC_D12 | None | Yes
PD | 11 | Digital I/O | None | None | None | None | TIM3_CH4 | FSMC_A16 | None | Yes
PD | 12 | Digital I/O | None | None | None | None | TIM4_CH1 | FSMC_A17 | None | Yes
PD | 13 | Digital I/O | None | None | None |  |  |  |  | Yes
PE | 0 | Digital I/O | None | None | None | None | TIM4_ETR | FSMC_NBL0 | None | Yes
PE | 1 | Digital I/O | None | None | None | None | TIM4_CH1 | FSMC_NBL1 | None | No | Red LED for warning
PE | 2 | Digital I/O | None | None | None | None | TIM3_CH1 | FSMC_A23 | ETH_MII_TXD3 | Yes
PE | 3 | Digital I/O | None | None | None | None | TIM3_CH2 | FSMC_A19 | None | No | SPI 1 Chip Select (Can Remove)
PE | 4 | Digital I/O | None | None | None | None | TIM3_CH3 | FSMC_A20 | None | Yes
PE | 5 | Digital I/O | None | None | None | None | TIM3_CH4 | FSMC_A21 | None | Yes
PE | 6 | Digital I/O | None | None | None | None | TIM4_CH1 | FSMC_A22 | None | Yes
PE | 7 | Digital I/O | None | None | None | None | None | FSMC_D4 | None | Yes
PE | 8 | Digital I/O | None | None | None | None | None | FSMC_D5 | None | Yes
PE | 9 | Digital I/O | None | None | None | None | None | FSMC_D6 | None | Yes
PE | 10 | Digital I/O | None | None | None | None | None | FSMC_D7 | None | Yes
PE | 11 | Digital I/O | None | None | None | None | None | FSMC_D8 | None | Yes
PE | 12 | Digital I/O | None | None | None | None | None | FSMC_D9 | None | Yes
PE | 13 | Digital I/O | None | None | None | None | None | FSMC_D10 | None | Yes
PE | 14 | Digital I/O | None | None | None | None | None | FSMC_D11 | None | Yes
PE | 15 | Digital I/O | None | None | None | None | None | FSMC_D12 | None | Yes
PH | 0 | Digital I/O | None | None | None | None | None | None | OSC_IN | Yes
PH | 1 | Digital I/O | None | None | None | None | None | None | OSC_OUT | Yes

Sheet: Commands
Commands | Function
&_START_* | Starts the system
STOP | Stops the system
&_CAL_PITCH_1_* | Starts calibration for rotor 1
&_CAL_PITCH_2_* | Starts calibration for rotor 2
&_SET_SPEED_speed_* | Sets the target angular velocity of the aircraft
&_SET_PITCH_pitch_* | Sets the target default pitch of the aircraft
&_SET_PID_p_i_d_* | Sets the P, I and D values for the controller
&_SET_DIR_direction_* | Sets the direction of the aircraft
 | 0: Hover
 | 1: Forward
 | 2: Backwards
 | 3: Left
 | 4: Right
&_SHW_PITCH_* | Displays the pitch in a User friendly format
&_SHW_RPM_* | Displays the angular velocity in a user friendly format
&_SHW_DATA_* | Displays data that gets sent for analysis
&_SHW_PWM_* | Shows the PWM of each motor
&_DBG_MODE_rotor 1 top motor_ rotor 1 bottom motor_rotor 2 top motor_rotor 2 bottom motor_* | A debugging option to control each motor wihout the need to start the system. This is used for checking individual motors. | Range 25 is off 100 is full power

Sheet: Results anaylsis
0 | 45 | 20 | 60 | 90
792.4439252 | 898.4018692 | 836.8878505 | 974.5514019 | 1131.808411
793 | 895 | 837 | 972 | 1135
791 | 897 | 840 | 975 | 1131
796 | 897 | 837 | 977 | 1133
794 | 901 | 837 | 977 | 1131
794 | 903 | 837 | 973 | 1133
792 | 913 | 835 | 975 | 1130
793 | 896 | 839 | 979 | 1131
792 | 896 | 836 | 975 | 1133 | 0 | 792.4439252
794 | 906 | 835 | 976 | 1133 | 20 | 836.8878505
793 | 901 | 837 | 971 | 1133 | 45 | 898.4018692
794 | 897 | 839 | 975 | 1129 | 60 | 974.5514019
792 | 897 | 837 | 977 | 1132 | 90 | 1131.808411
790 | 909 | 838 | 973 | 1133
793 | 900 | 835 | 971 | 1135
796 | 905 | 837 | 973 | 1133
793 | 896 | 835 | 972 | 1131
793 | 900 | 837 | 973 | 1129
793 | 871 | 835 | 976 | 1134
791 | 897 | 837 | 977 | 1100
796 | 900 | 837 | 973 | 1131
794 | 899 | 809 | 973 | 1133
791 | 889 | 836 | 991 | 1133
793 | 899 | 837 | 975 | 1131
796 | 902 | 839 | 974 | 1131
792 | 899 | 837 | 972 | 1144
789 | 900 | 837 | 974 | 1131
794 | 901 | 838 | 977 | 1132
793 | 897 | 837 | 975 | 1136
795 | 901 | 837 | 972 | 1131
791 | 905 | 836 | 977 | 1133
791 | 893 | 846 | 972 | 1110
795 | 900 | 832 | 972 | 1133
795 | 900 | 840 | 977 | 1129
791 | 901 | 838 | 970 | 1133
793 | 899 | 837 | 975 | 1127
793 | 898 | 837 | 969 | 1131
788 | 907 | 837 | 975 | 1130
793 | 899 | 832 | 972 | 1133
794 | 900 | 833 | 975 | 1145
793 | 897 | 836 | 973 | 1131
793 | 899 | 835 | 993 | 1133
792 | 898 | 839 | 973 | 1133
792 | 899 | 836 | 975 | 1139
795 | 900 | 840 | 974 | 1133
793 | 897 | 851 | 975 | 1129
796 | 899 | 835 | 975 | 1133
794 | 913 | 837 | 974 | 1133
793 | 899 | 836 | 973 | 1132
794 | 900 | 837 | 971 | 1133
792 | 904 | 837 | 973 | 1129
792 | 899 | 835 | 975 | 1133
797 | 905 | 831 | 962 | 1130
792 | 899 | 836 | 975 | 1133
790 | 901 | 837 | 973 | 1133
793 | 900 | 837 | 976 | 1125
793 | 900 | 837 | 975 | 1133
793 | 859 | 838 | 989 | 1136
792 | 897 | 837 | 975 | 1145
793 | 900 | 837 | 984 | 1133
792 | 901 | 837 | 982 | 1130
793 | 896 | 836 | 976 | 1133
794 | 905 | 837 | 977 | 1137
792 | 898 | 835 | 973 | 1132
789 | 901 | 840 | 975 | 1129
793 | 899 | 837 | 975 | 1133
793 | 881 | 837 | 974 | 1132
793 | 901 | 837 | 975 | 1136
794 | 872 | 837 | 973 | 1129
793 | 897 | 837 | 975 | 1135
792 | 897 | 838 | 975 | 1131
792 | 899 | 836 | 955 | 1135
775 | 899 | 837 | 973 | 1131
793 | 898 | 840 | 976 | 1132
789 | 900 | 837 | 977 | 1131
793 | 899 | 837 | 975 | 1133
791 | 900 | 836 | 973 | 1129
797 | 900 | 851 | 973 | 1132
793 | 897 | 833 | 976 | 1133
792 | 899 | 839 | 966 | 1132
793 | 905 | 839 | 973 | 1132
793 | 901 | 837 | 976 | 1133
792 | 899 | 837 | 974 | 1132
793 | 903 | 836 | 973 | 1133
791 | 896 | 835 | 976 | 1131
795 | 897 | 844 | 976 | 1133
793 | 897 | 837 | 973 | 1131
793 | 900 | 837 | 973 | 1129
795 | 899 | 839 | 975 | 1133
793 | 897 | 837 | 973 | 1132
792 | 910 | 839 | 975 | 1129
764 | 899 | 853 | 973 | 1132
793 | 905 | 837 | 973 | 1131
759 | 894 | 839 | 978 | 1125
798 | 900 | 837 | 973 | 1137
793 | 899 | 835 | 977 | 1128
793 | 845 | 835 | 973 | 1131
794 | 897 | 837 | 977 | 1132
790 | 902 | 836 | 976 | 1141
791 | 898 | 836 | 976 | 1131
794 | 865 | 836 | 975 | 1131
793 | 899 | 838 | 975 | 1132
796 | 901 | 836 | 976 | 1131
794 | 893 | 837 | 980 | 1131
793 | 905 | 837 | 975 | 1132
793 | 896 | 836 | 973 | 1129
792 | 893 | 836 | 975 | 1132
793 | 864 | 836 | 975 | 1131
795 | 899 | 843 | 972 | 1135
794 | 897 | 837 | 977 | 1129
792 | 897 | 838 | 977 | 1132
792 | 898 | 837 | 973 | 1132
793 | 904 | 837 | 972 | 1133
792 | 869 | 839 | 974 | 1134
792 | 900 | 837 | 977 | 1131
790 | 900 | 837 | 975 | 1122
791 | 900 | 836 | 977 | 1130
793 | 903 | 836 | 975 | 1129
792 | 899 | 837 | 971 | 1133
791 | 909 | 837 | 973 | 1129
795 | 899 | 835 | 974 | 1131
793 | 900 | 839 | 975 | 1133
793 | 911 | 837 | 973 | 1133
794 | 901 | 837 | 975 | 1131
793 | 898 | 838 | 974 | 1131
793 | 899 | 836 | 983 | 1131
793 | 900 | 833 | 973 | 1149
796 | 912 | 836 | 976 | 1133
793 | 880 | 835 | 975 | 1131
793 | 898 | 837 | 981 | 1129
793 | 896 | 837 | 973 | 1133
793 | 901 | 837 | 973 | 1130
795 | 901 | 837 | 975 | 1133
793 | 899 | 840 | 975 | 1135
793 | 904 | 836 | 975 | 1131
793 | 899 | 835 | 975 | 1128
792 | 901 | 837 | 976 | 1145
794 | 900 | 835 | 975 | 1130
792 | 897 | 835 | 976 | 1129
793 | 900 | 838 | 973 | 1132
789 | 897 | 838 | 968 | 1131
795 | 919 | 837 | 976 | 1133
791 | 901 | 837 | 976 | 1129
790 | 899 | 836 | 973 | 1133
793 | 905 | 837 | 973 | 1125
793 | 901 | 837 | 976 | 1131
793 | 898 | 837 | 973 | 1131
793 | 900 | 838 | 977 | 1129
795 | 903 | 839 | 973 | 1135
792 | 900 | 837 | 975 | 1133
793 | 896 | 836 | 976 | 1129
792 | 899 | 840 | 973 | 1135
793 | 901 | 838 | 976 | 1132
793 | 899 | 836 | 977 | 1133
793 | 897 | 839 | 976 | 1132
792 | 899 | 837 | 973 | 1135
793 | 901 | 839 | 976 | 1128
793 | 901 | 836 | 973 | 1135
793 | 897 | 837 | 975 | 1129
793 | 901 | 837 | 969 | 1135
792 | 899 | 837 | 974 | 1131
791 | 900 | 844 | 973 | 1132
793 | 897 | 817 | 973 | 1140
792 | 903 | 837 | 975 | 1131
793 | 901 | 839 | 976 | 1131
793 | 898 | 837 | 975 | 1131
792 | 895 | 837 | 977 | 1133
792 | 903 | 839 | 976 | 1132
793 | 901 | 837 | 975 | 1131
792 | 901 | 837 | 973 | 1132
793 | 898 | 837 | 976 | 1136
793 | 899 | 837 | 974 | 1132
792 | 899 | 827 | 976 | 1133
793 | 901 | 837 | 973 | 1131
792 | 900 | 836 | 973 | 1135
795 | 900 | 837 | 975 | 1131
793 | 899 | 838 | 979 | 1133
792 | 869 | 837 | 975 | 1132
793 | 898 | 837 | 976 | 1133
792 | 900 | 832 | 976 | 1132
794 | 895 | 839 | 975 | 1129
795 | 899 | 835 | 975 | 1127
792 | 899 | 835 | 978 | 1131
792 | 899 | 837 | 978 | 1137
793 | 901 | 837 | 974 | 1130
791 | 897 | 837 | 973 | 1132
793 | 901 | 837 | 974 | 1133
792 | 899 | 836 | 977 | 1131
794 | 901 | 831 | 974 | 1133
793 | 900 | 839 | 973 | 1133
795 | 899 | 834 | 973 | 1129
791 | 899 | 836 | 973 | 1131
793 | 899 | 837 | 975 | 1131
791 | 901 | 837 | 981 | 1131
793 | 901 | 832 | 971 | 1133
792 | 900 | 836 | 974 | 1129
785 | 895 | 837 | 975 | 1129
794 | 901 | 837 | 975 | 1135
793 | 898 | 837 | 934 | 1133
792 | 896 | 838 | 973 | 1132
792 | 898 | 837 | 975 | 1129
792 | 900 | 836 | 977 | 1133
791 | 900 | 837 | 977 | 1133
794 | 899 | 837 | 973 | 1130
793 | 904 | 837 | 975 | 1137
792 | 900 | 840 | 973 | 1132
793 | 900 | 837 | 977 | 1131
793 | 901 | 837 | 973 | 1130
792 | 897 | 837 | 975 | 1112
793 | 899 | 836 | 977 | 1133
793 | 901 | 835 | 975 | 1132
793 | 917 | 839 | 975 | 1131
793 | 897 | 839 | 975 | 1136
796 | 893 | 837 | 976 | 1129
793 | 897 | 840 | 973 | 1133
 | 895 | 837 | 970 | 1129
 | 935 | 837 | 977 | 1132
 | 898 | 837 | 975 | 1133
 | 900 | 851 | 973 | 1133
 | 899 | 835 | 977 | 1130
 | 897 | 838 | 974 | 1129
 | 900 | 837 | 975 | 1131
 | 900 | 837 | 975 | 1128
 | 899 | 833 | 977 | 1132
 | 891 | 836 | 975 | 1132
 | 900 | 841 | 975 | 1133
 | 897 | 837 | 973 | 1132
 | 900 | 837 | 975 | 1133
 | 900 | 837 | 973 | 1133
 | 899 | 818 | 975 | 1132
 | 909 | 837 | 973 | 1131
 | 900 | 835 | 973 | 1135
 | 899 | 847 | 975 | 1131
 | 895 | 833 | 988 | 1133
 | 941 | 838 | 952 | 1133
 | 898 | 837 | 977 | 1131
 | 901 | 837 | 983 | 1133
 | 899 | 836 | 995 | 1133
 | 901 | 837 | 976 | 1128
 | 900 | 837 | 975 | 1132
 | 901 | 838 | 973 | 1135
 | 901 | 845 | 975 | 1132
 | 915 | 837 | 975 | 1144
 | 901 | 839 | 976 | 1132
 | 899 | 838 | 975 | 1139
 | 899 | 839 | 973 | 1133
 | 901 | 837 | 975 | 1133
 | 900 | 833 | 975 | 1137
 | 900 | 837 | 975 | 1131
 | 900 | 832 | 975 | 1132
 | 901 | 837 | 973 | 1136
 | 905 | 837 | 975 | 1133
 | 897 | 837 | 973 | 1131
 | 875 | 835 | 973 | 1130
 | 911 | 837 | 977 | 1130
 | 901 | 837 | 975 | 1129
 | 901 | 835 | 974 | 1133
 | 898 | 837 | 973 | 1131
 | 899 | 837 | 973 | 1129
 | 913 | 861 | 975 | 1133
 | 900 | 837 | 975 | 1131
 | 899 | 853 | 973 | 1132
 | 897 | 834 | 973 | 1131
 | 901 | 835 | 973 | 1133
 | 896 | 837 | 971 | 1130
 | 899 | 836 | 975 | 1134
 | 901 | 837 | 973 | 1133
 | 899 | 837 | 971 | 1129
 | 897 | 837 | 976 | 1135
 | 897 | 833 | 973 | 1131
 | 899 | 836 | 973 | 1129
 | 897 | 830 | 973 | 1140
 | 898 | 837 | 975 | 1133
 | 900 | 837 | 969 | 1129
 | 901 | 835 | 975 | 1130
 | 897 | 837 | 973 | 1134
 | 897 | 835 | 973 | 1131
 | 899 | 839 | 977 | 1131
 | 899 | 847 | 988 | 1128
 |  | 837 | 973 | 1131
 |  | 836 | 975 | 1132
 |  | 837 | 973 | 1131
 |  | 839 | 973 | 1132
 |  | 837 | 975 | 1129
 |  | 838 | 975 | 1124
 |  | 835 | 975 | 1130
 |  | 841 | 977 | 1131
 |  | 820 | 977 | 1133
 |  | 837 | 973 | 1132
 |  | 837 | 975 | 1132
 |  | 837 | 977 | 1131
 |  | 836 | 973 | 1132
 |  | 835 | 973 | 1123
 |  | 835 | 973 | 1140
 |  | 837 | 977 | 1130
 |  | 842 | 973 | 1139
 |  | 837 | 973 | 1131
 |  | 836 | 956 | 1131
 |  | 836 | 992 | 1131
 |  | 837 | 973 | 1133
 |  | 837 | 977 | 1131
 |  | 837 | 973 | 1131
 |  | 834 | 975 | 1128
 |  | 836 | 973 | 1133
 |  | 839 | 973 | 1132
 |  | 837 | 968 | 1131
 |  | 833 | 975 | 1131
 |  | 847 | 975 | 1133
 |  | 837 | 974 | 1129
 |  | 837 | 973 | 1133
 |  | 837 | 973 | 1132
 |  | 837 | 973 | 1131
 |  | 839 | 973 | 1131
 |  | 838 | 977 | 1132
 |  | 837 | 973 | 1131
 |  | 811 | 949 | 1133
 |  | 835 | 973 | 1130
 |  | 853 | 975 | 1132
 |  | 837 | 976 | 1132
 |  | 837 | 972 | 1131
 |  | 840 | 973 | 1131
 |  | 836 | 977 | 1133
 |  | 837 | 974 | 1134
 |  | 839 | 975 | 1135
 |  | 837 | 975 | 1130
 |  | 837 | 974 | 1131
 |  | 835 | 979 | 1131
 |  | 837 | 973 | 1132
 |  | 837 | 977 | 1134
 |  | 837 | 973 | 1134
 |  | 838 | 973 | 1129
 |  | 837 | 973 | 1134
 |  | 837 | 973 | 1136
 |  | 835 | 973 | 1133
 |  | 841 | 975 | 1134
 |  | 839 | 973 | 1129
 |  | 835 | 973 | 1129
 |  | 837 | 975 | 1127
 |  | 837 | 977 | 1129
 |  | 837 | 977 | 1131
 |  | 837 | 973 | 1131
 |  | 837 | 975 | 1131
 |  | 839 | 976 | 1128
 |  | 836 | 943 | 1133
 |  | 840 | 975 | 1128
 |  | 836 | 975 | 1130
 |  | 837 | 977 | 1130
 |  | 837 | 973 | 1132
 |  | 813 | 974 | 1131
 |  | 836 | 973 | 1133
 |  | 837 | 975 | 1133
 |  | 837 | 972 | 1131
 |  | 837 | 973 | 1133
 |  | 837 | 972 | 1133
 |  | 835 | 973 | 1132
 |  | 837 | 973 | 1129
 |  | 836 | 973 | 1129
 |  | 849 | 975 | 1133
 |  | 837 | 975 | 1130
 |  | 865 | 973 | 1131
 |  | 839 | 975 | 1137
 |  | 839 | 973 | 1132
 |  | 837 | 975 | 1132
 |  | 836 | 973 | 1133
 |  | 836 | 973 | 1131
 |  | 840 | 973 | 1133
 |  | 837 | 973 | 1130
 |  | 837 | 975 | 1131
 |  | 837 |  | 1129
 |  | 845 |  | 1129
 |  | 837 |  | 1140
 |  | 837 |  | 1132
 |  | 837 |  | 1129
 |  | 837 |  | 1133
 |  | 836 |  | 1131
 |  | 835 |  | 1131
 |  | 833 |  | 1132
 |  | 837 |  | 1129
 |  | 837 |  | 1132
 |  | 837 |  | 1132
 |  | 837 |  | 1137
 |  | 837 |  | 1128
 |  | 836 |  | 1132
 |  | 835 |  | 1133
 |  | 837 |  | 1129
 |  | 837 |  | 1129
 |  | 837 |  | 1131
 |  | 839 |  | 1135
 |  | 836 |  | 1131
 |  | 832 |  | 1129
 |  | 836 |  | 1132
 |  | 837 |  | 1133
 |  | 836 |  | 1138
 |  | 839 |  | 1131
 |  | 837 |  | 1131
 |  | 837 |  | 1132
 |  | 837 |  | 1129
 |  | 837 |  | 1137
 |  | 836 |  | 1126
 |  | 837 |  | 1128
 |  | 837 |  | 1133
 |  | 837 |  | 1133
 |  | 839 |  | 1132
 |  | 837 |  | 1131
 |  | 837 |  | 1131
 |  | 836 |  | 1128
 |  | 833 |  | 1133
 |  | 839 |  | 1133
 |  | 838 |  | 1133
 |  | 839 |  | 1131
 |  | 839 |  | 1129
 |  | 836 |  | 1133
 |  | 833 |  | 1131
 |  | 836 |  | 1132
 |  | 839 |  | 1131
 |  | 837 |  | 1130
 |  | 837 |  | 1133
 |  | 831 |  | 1132
 |  | 837 |  | 1129
 |  | 839 |  | 1140
 |  | 838 |  | 1133
 |  | 839 |  | 1133
 |  | 837 |  | 1129
 |  | 838 |  | 1132
 |  | 843 |  | 1133
 |  | 837 |  | 1132
 |  | 835 |  | 1131
 |  | 837 |  | 1133
 |  | 835 |  | 1132
 |  | 840 |  | 1133
 |  | 838 |  | 1129
 |  | 837 |  | 1131
 |  | 835 |  | 1131
 |  | 837 |  | 1133
 |  | 837 |  | 1131
 |  | 837 |  | 1131
 |  | 835 |  | 1131
 |  | 836 |  | 1131
 |  | 837 |  | 1130
 |  | 836 |  | 1132
 |  | 837 |  | 1133
 |  | 837 |  | 1131
 |  | 837 |  | 1131
 |  | 839 |  | 1125
 |  | 836 |  | 1133
 |  | 839 |  | 1129
 |  | 832 |  | 1132
 |  | 839 |  | 1129
 |  | 835 |  | 1131
 |  | 836 |  | 1132
 |  | 839 |  | 1133
 |  | 844 |  | 1129
 |  | 838 |  | 1129
 |  | 839 |  | 1135
 |  | 837 |  | 1130
 |  | 837 |  | 1133
 |  | 836 |  | 1131
 |  | 837 |  | 1137
 |  | 837 |  | 1132
 |  | 837 |  | 1131
 |  | 839 |  | 1131
 |  | 837 |  | 1131
 |  | 841 |  | 1131
 |  | 840 |  | 1132
 |  | 839 |  | 1128
 |  | 834 |  | 1131
 |  | 837 |  | 1132
 |  | 836 |  | 1136
 |  | 839 |  | 1134
 |  | 836 |  | 1133
 |  | 838 |  | 1133
 |  | 839 |  | 1133
 |  | 835 |  | 1131
 |  | 843 |  | 1133
 |  | 833 |  | 1132
 |  | 837 |  | 1132
 |  | 837 |  | 1131
 |  | 837 |  | 1131
 |  | 837 |  | 1135
 |  | 849 |  | 1132
 |  | 837 |  | 1130
 |  | 840 |  | 1133
 |  | 839 |  | 1132
 |  | 837 |  | 1131
 |  | 835 |  | 1131
 |  | 834 |  | 1130
 |  | 836 |  | 1130
 |  | 837 |  | 1133
 |  | 839 |  | 1133
 |  | 835 |  | 1133
 |  | 837 |  | 1132
 |  | 836 |  | 1131
 |  | 835 |  | 1130
 |  | 838 |  | 1130
 |  | 836 |  | 1132
 |  | 836 |  | 1130
 |  | 863 |  | 1126
 |  | 837 |  | 1130
 |  | 840 |  | 1132
 |  | 837 |  | 1131
 |  | 839 |  | 1132
 |  | 837 |  | 1131
 |  | 835 |  | 1131
 |  | 837 |  | 1133
 |  | 836 |  | 1131
 |  | 837 |  | 1133
 |  | 836 |  | 1133
 |  | 837 |  | 1129
 |  | 836 |  | 1129
 |  | 836 |  | 1131
 |  | 837 |  | 1133
 |  | 837 |  | 1130
 |  | 837 |  | 1130
 |  | 837 |  | 1129
 |  | 836 |  | 1129
 |  | 836 |  | 1131
 |  | 837 |  | 1131
 |  | 839 |  | 1131
 |  | 853 |  | 1132
 |  | 837 |  | 1131
 |  | 841 |  | 1130
 |  | 837 |  | 1136
 |  | 839 |  | 1129
 |  | 836 |  | 1131
 |  | 837 |  | 1131
 |  | 837 |  | 1133
 |  | 815 |  | 1129
 |  | 836 |  | 1130
 |  | 837 |  | 1133
 |  | 838 |  | 1131
 |  | 839 |  | 1132
 |  | 840 |  | 1137
 |  | 836 |  | 1129
 |  | 835 |  | 1132
 |  | 835 |  | 1131
 |  | 845
 |  | 837
 |  | 836
 |  | 833
 |  | 833
 |  | 836
 |  | 835
 |  | 836
 |  | 838
 |  | 834
 |  | 837
 |  | 838
 |  | 837
 |  | 836
 |  | 837
 |  | 837
 |  | 832
 |  | 836
 |  | 839
 |  | 836
 |  | 836
 |  | 834
 |  | 836
 |  | 838
 |  | 837
 |  | 836
 |  | 837
 |  | 837
 |  | 837
 |  | 839
 |  | 836
 |  | 841
 |  | 840
 |  | 836
 |  | 839
 |  | 841
 |  | 837
 |  | 836
 |  | 836
 |  | 837
 |  | 836
 |  | 852
 |  | 837
 |  | 840
 |  | 833
 |  | 837
 |  | 837
 |  | 836
 |  | 836
 |  | 836
 |  | 837
 |  | 837
 |  | 836
 |  | 837
 |  | 837
 |  | 839
 |  | 839

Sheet: Lift Analysis
Column1 | Pitch | Column2
0 120.1 | 0 | 0.6453 | 30 | 20 30.1 | 18 | 0.6912 | 50 | 0.5 | 0.1789 | 0.2542113696 | 0.08331826039 |  | 171.8997192%
0 120.2 | -5 | 0.0643 | 60 | 20 60.1 | ~20 | 1.3008 | 81 | 1.3 |  | 1.016845478 | 0.3332730416 | 1.5 | 27.9250415%
0 150.1 | -5 | 1.2849 | 90 | 20 90.1 | 22 | 2.7306 | 116 | 2.73 |  | 2.287902326 | 0.7498643435 | 2.7 | 19.34950058%
0 150.2 | 2.5 | 0.067 | 120 | 20 120.2 | 17.5 | 4.3901 | 148 | 4.39 |  | 4.067381913 | 1.333092166 | 3.2 | 7.934295178%
0 180.1 | ~-5 | 0.0896 | 150 | 20 150.1 | 17.5 | 5.5427 | 167 | 5.5 |  | 6.355284239 | 2.08295651 |  | 12.78596218%
0 180.2 | -10 | 0.008 | 180 |  |  |  |  |  |  | 9.151609304 | 2.999457374
0 30.1 | 15 | 0.76 | 220 |  |  |  |  |  |  | 9.58031533 | 4.480670892
0 30.2 | 7.5 | 0.5237
0 60.1 | 5 | 1.1377
0 60.2 | 5 | 1.1566
0 90.1 | 5 | 1.6736 | 30 | 20 30.2 | 17.5 | 0.7633 | 0.1781463594
0 90.2 | 5 | 1.693 | 60 | 10 60.2 | 15 | 1.1823 | 1.132540253
10 120.1 | 5 10 | 2.0367 | 90 | 10 90.1 | 10 | 2.5678 | 2.27889672
10 120.2 | 0 | 0.9876 | 120 | 20 120.2 | 17.5 | 4.3901 | 2.850341751
10 150.1 | 5 10 | 2.0477 | 150 | 20 150.1 | 17.5 | 5.5427 | 4.453658986
10 150.2 | 5 | 1.7126 | 180 | 20 180.2 | 7.5 | 4.7438 | 6.41326894
10 180.1 | -2.5 | 0.0737
10 180.2 | -5 | -0.0305
10 30.1 | 32.5 | 0.5848
10 30.2 | 17.5 | 0.3046 | 30 | 0 30.2 | 7.5 | 0.5237 | 0.04015419059 | 0.015742489
10 60.1 | 15 | 1.1823 | 60 | 0 60.1 | 5 | 1.1377 | 0.1606167624 | 0.062969956
10 60.2 | 15 | 1.2553 | 90 | 0 90.2 | 5 | 1.693 | 0.3613877153 | 0.141682401
10 90.1 | 10 | 2.7303 | 120 | 10 120.1 | 5 10 | 2.0367 | 0.6424670495 | 0.251879824
10 90.2 | 10 | 2.5678 | 150 | 10 150.2 | 5 | 1.7126 | 1.003854765 | 0.393562225
20 120.1 | 15 20 | 3.7614 | 180 | 20 180.2 | 7.5 | 4.7438 | 1.445550861 | 0.566729604
20 120.2 | 17.5 | 4.3901 | 200 |  |  |  | 1.784630693 | 0.6996661778
20 150.1 | 17.5 | 5.5427 | 220 |  |  |  | 2.159403138 | 0.8465960752
20 150.2 | 0 | 3.5893
20 180.1 | 7.5 | 4.4026
20 180.2 | 7.5 | 4.7438
20 30.1 | 18 | 0.6912
20 30.2 | 17.5 | 0.7633
20 60.1 | ~20 | 1.3008
20 60.2 | 23 | 1.3969
20 90.1 | 22 | 2.7306
20 90.2 | ~20 | 2.8483

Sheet: Nucleo Board
Pin
PC7 | SPI1_CE
PB13 | LED
PA5 | SPI1_SCK
PA6 | SPI1_MISO
PA7 | SPI1_MOSI
PB6 | SPI1_CSN
PB12 | DT_LC_1
PB13 | SCK_LC_1
PB14 | DT_LC_2
PB15 | SCK_LC_2
PC6 | DT_LC_3
PC7 | SCK_LC_3
PC8 | DT_LC_4
PC9 | SCK_LC_4

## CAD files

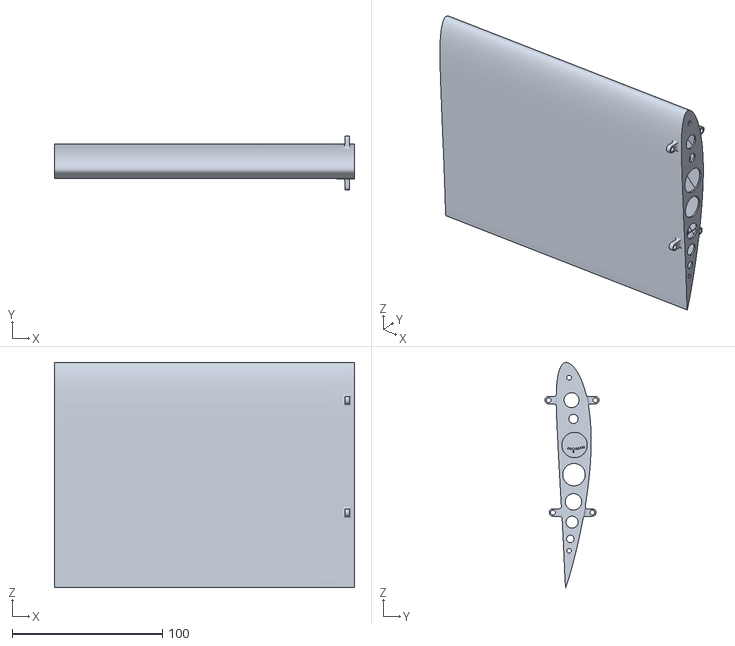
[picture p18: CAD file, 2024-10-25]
Skripsie/3D Prints/Light_NACA4415_Tip_Thrust.stl
200.0 x 36.1 x 150.0

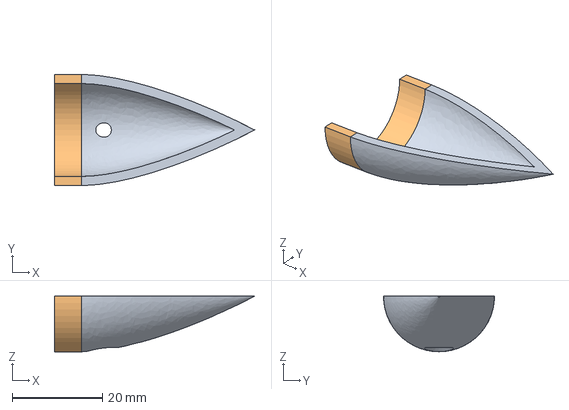
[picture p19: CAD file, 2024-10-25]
Skripsie/Rayde Krüger 3D Print Files-24723061/Motor_Mount_Top_Cover.stp
44.2 x 24.6 x 12.3 mm

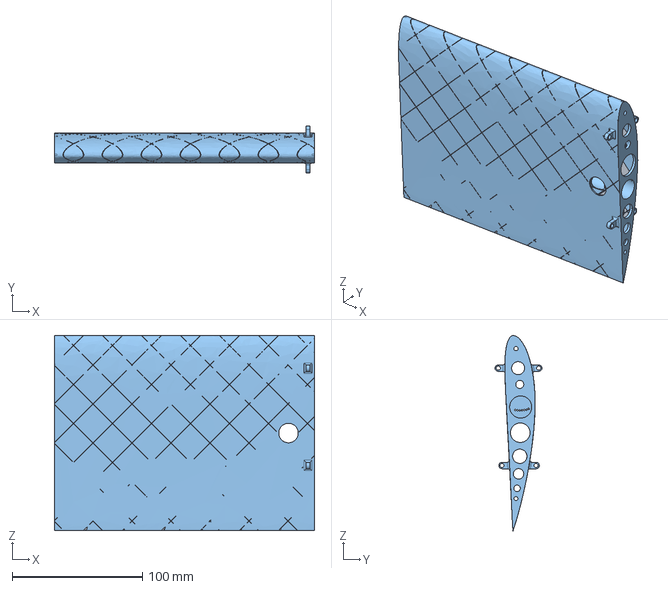
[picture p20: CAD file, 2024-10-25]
Skripsie/Rayde Krüger 3D Print STEP files -24723061/Tip-Thrust Rotor Segment.stp
200.0 x 36.1 x 150.0 mm

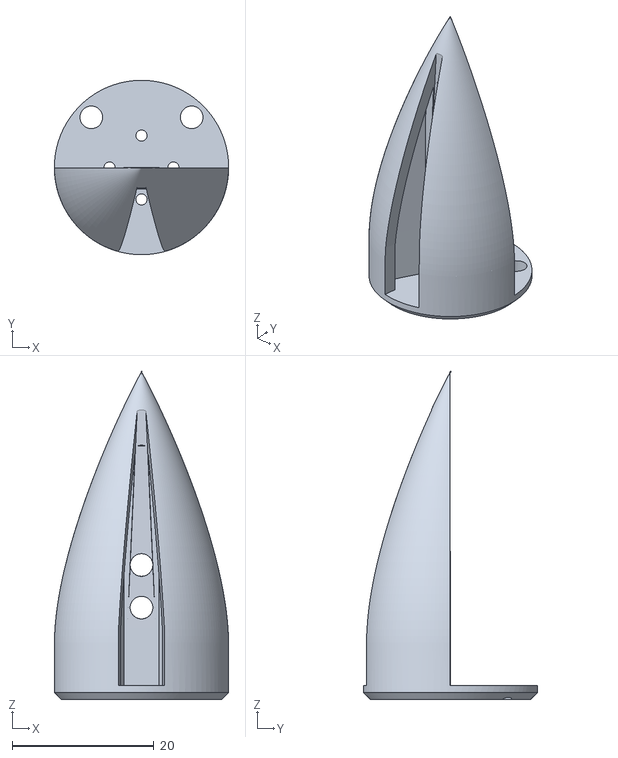
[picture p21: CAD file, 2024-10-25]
Skripsie/3D Prints/Motor_Mount.stl
24.6 x 24.6 x 46.2

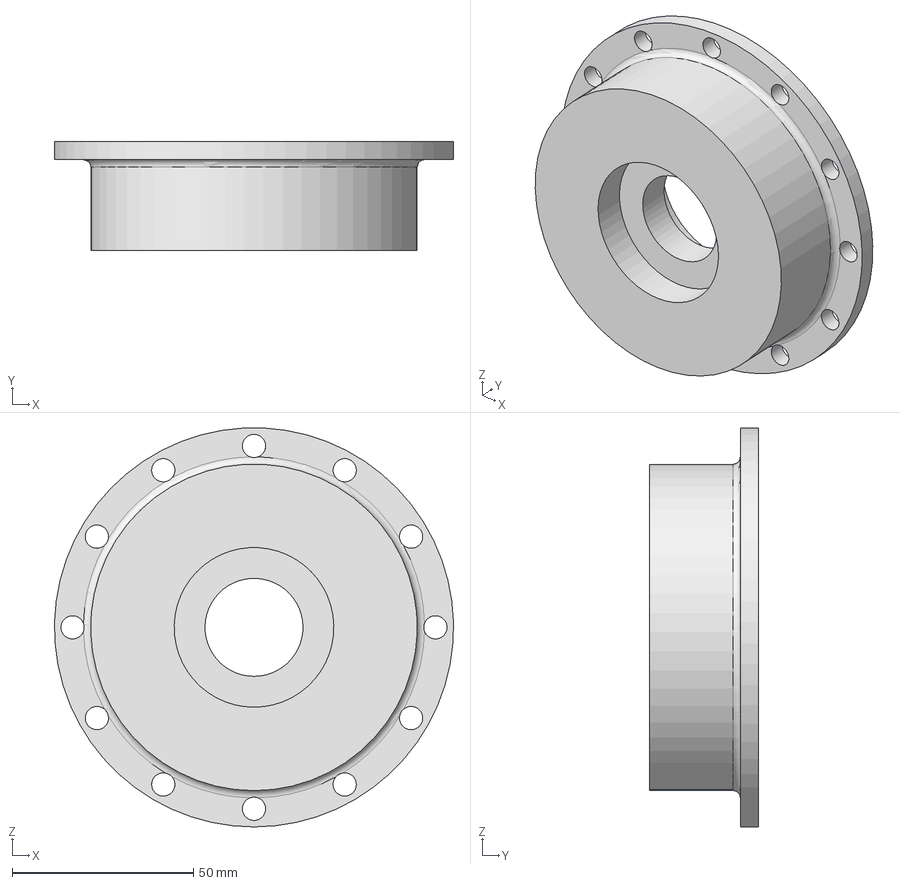
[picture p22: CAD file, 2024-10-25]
Skripsie/Rayde Krüger 3D Print Files-24723061/Hub_Connection.stp
110.0 x 30.0 x 109.9 mm

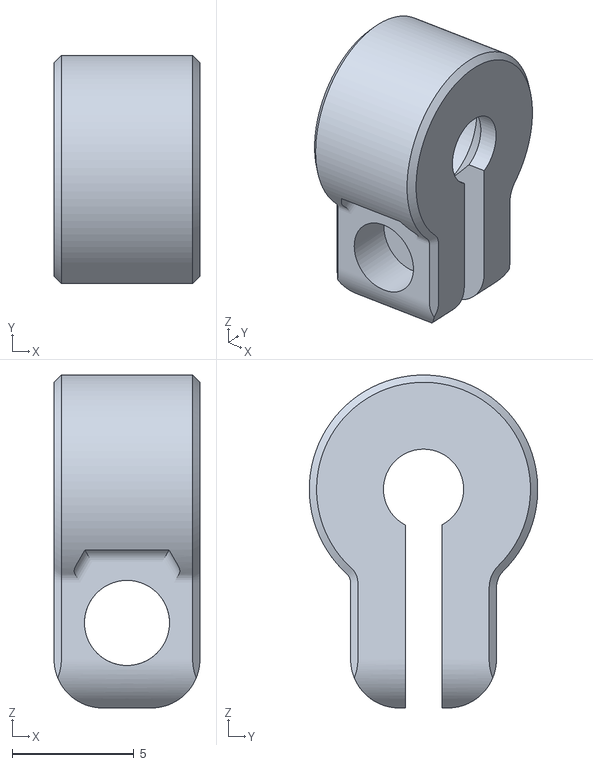
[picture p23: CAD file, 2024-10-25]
Skripsie/3D Prints/Pot_Interface_RevC.stl
6.00 x 9.40 x 13.7

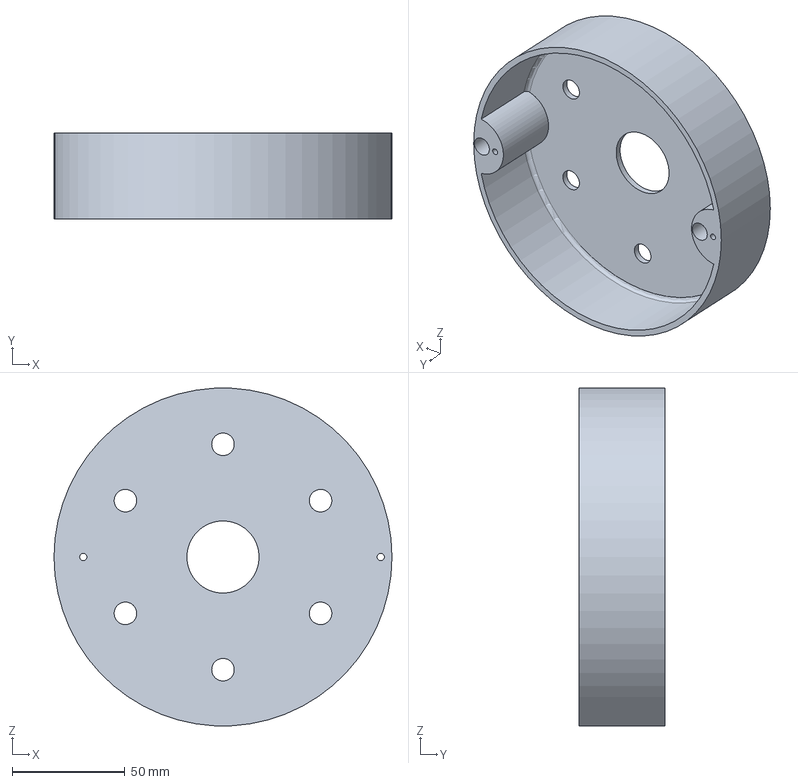
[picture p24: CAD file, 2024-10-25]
Skripsie/Rayde Krüger 3D Print Files-24723061/Electronics_Hub.stp
150.0 x 38.0 x 149.8 mm

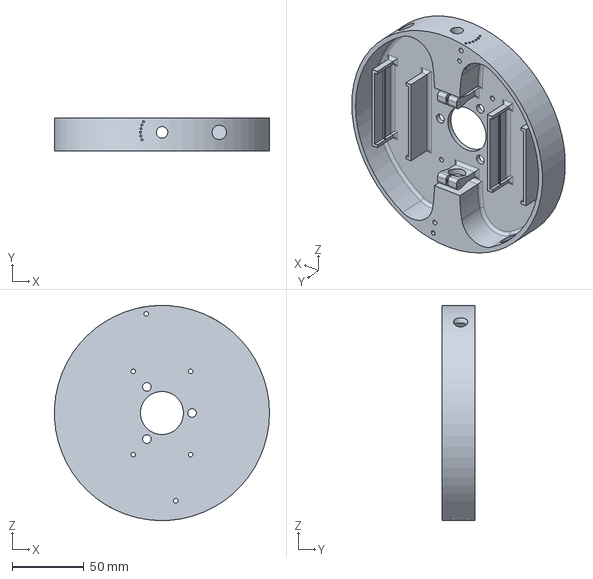
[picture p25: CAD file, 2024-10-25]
Skripsie/Rayde Krüger 3D Print STEP files -24723061/Hub level 1.stp
149.9 x 23.0 x 150.0 mm

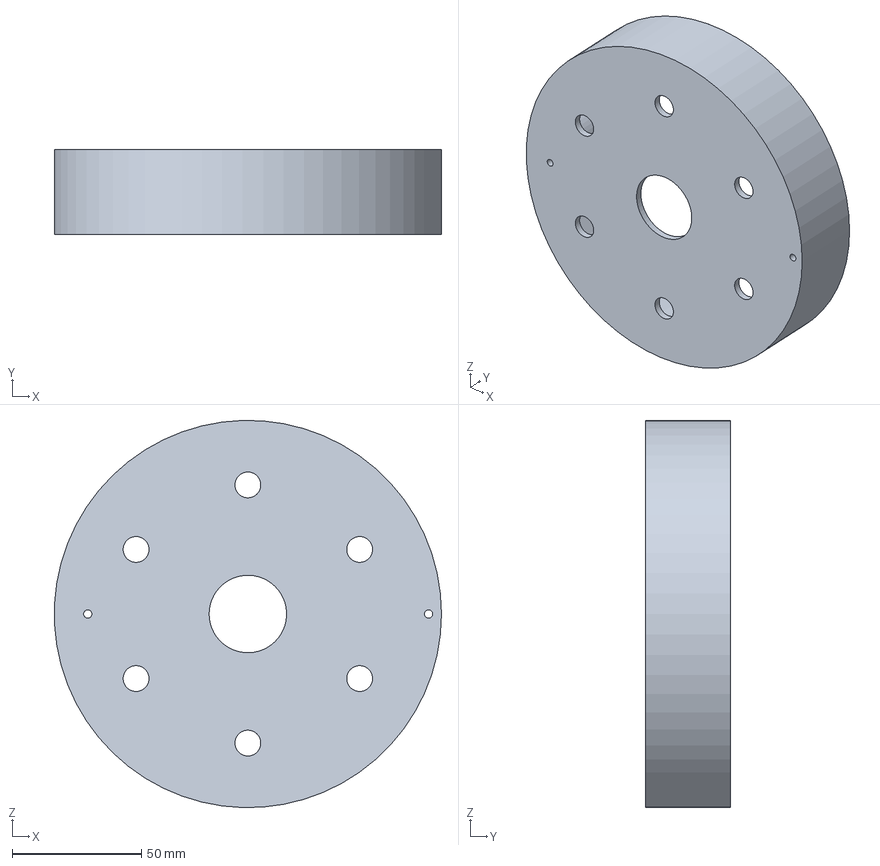
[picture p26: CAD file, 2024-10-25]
Skripsie/Rayde Krüger 3D Print STEP files -24723061/Hub level 2.stp
149.9 x 33.0 x 149.9 mm

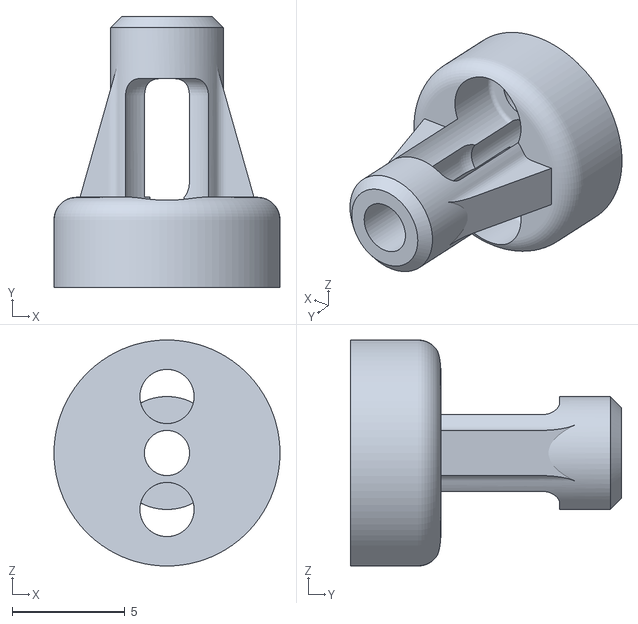
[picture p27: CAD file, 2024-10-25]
Skripsie/3D Prints/Prop Adapter Insert Final.stl
10.0 x 12.0 x 10.00

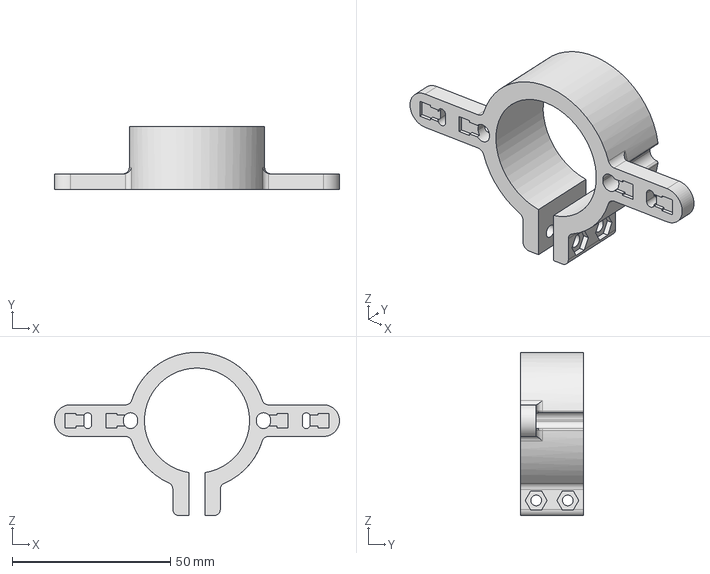
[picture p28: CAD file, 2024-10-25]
Skripsie/Rayde Krüger 3D Print Files-24723061/Hall_Effect_Sensor_Holder.stp
90.0 x 20.0 x 51.6 mm

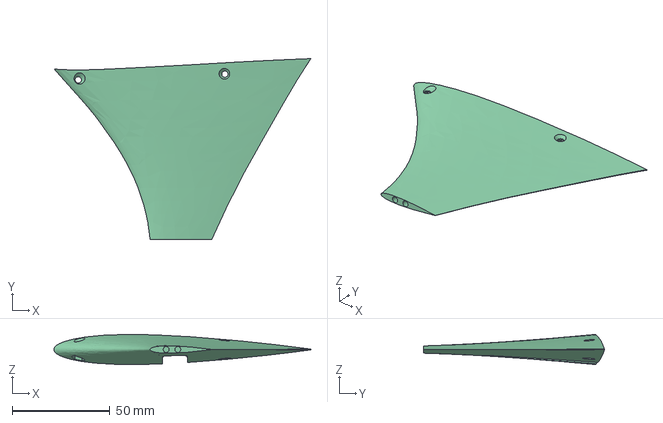
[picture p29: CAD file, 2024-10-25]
Skripsie/Rayde Krüger 3D Print STEP files -24723061/Bottom Motor Mount.stp
131.3 x 92.4 x 15.4 mm

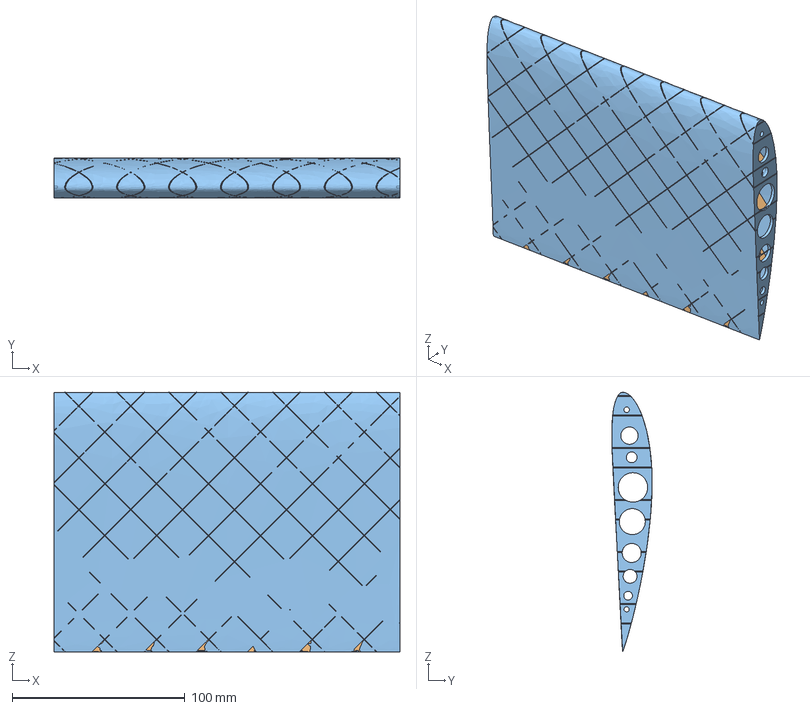
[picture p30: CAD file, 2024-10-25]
Skripsie/Rayde Krüger 3D Print STEP files -24723061/Rotor Segment Rev A.stp
200.0 x 23.3 x 150.0 mm

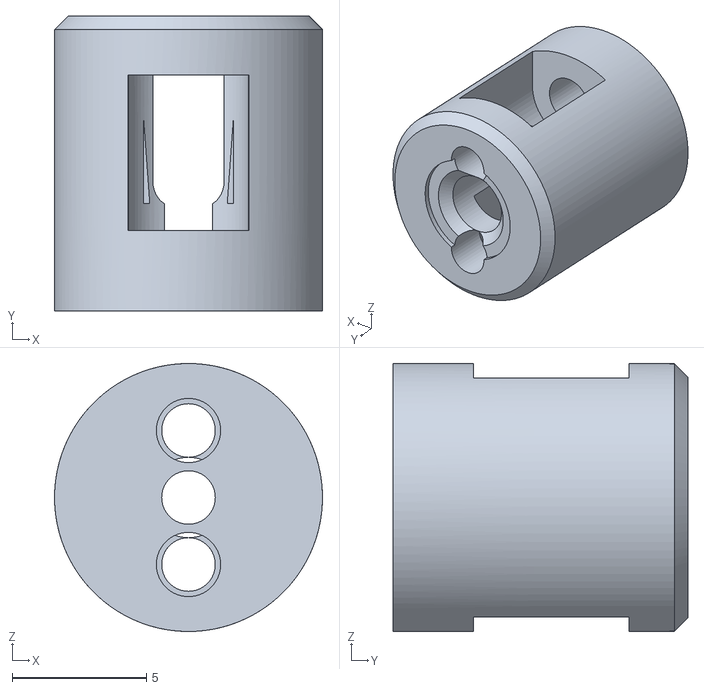
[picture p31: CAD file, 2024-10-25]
Skripsie/3D Prints/Prop Adapter Insert RevD.stl
10.0 x 11.0 x 10.00

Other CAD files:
Skripsie/Rayde Krüger 3D Print STEP files -24723061/Tip-Thrust Rotor Segment Rev A.stp
Skripsie/Rayde Krüger 3D Print Files-24723061/Motor_Mount_Bottom.stp
Skripsie/Rayde Krüger 3D Print STEP files -24723061/Top Motor Mount.stp
Skripsie/Rayde Krüger 3D Print STEP files -24723061/Rotor Segment.stp
Skripsie/3D Prints/Bottom_Pylon_200.stl
Skripsie/3D Prints/Hall_Effect_Sensor_Holder.stl
Skripsie/3D Prints/HubCovring.stl
Skripsie/3D Prints/Hub_Connection.stl
Skripsie/3D Prints/Hub_Level_2.stl
Skripsie/3D Prints/Hub_Test.stl
Skripsie/3D Prints/Light_NACA4415.stl
Skripsie/3D Prints/Light_NACA4415_Cut_through.stl
Skripsie/3D Prints/Light_NACA4415_Tip_Thrust_Supported.stl
Skripsie/3D Prints/Light_NACA4415_Tip_Thrust_Top.stl
Skripsie/3D Prints/Motor_Mount_Clip_on.stl
Skripsie/3D Prints/Motor_Mount_Clip_on_Cover.stl
Skripsie/3D Prints/Motor_Mount_RevA.stl
Skripsie/3D Prints/Motor_Mount_RevB.stl
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

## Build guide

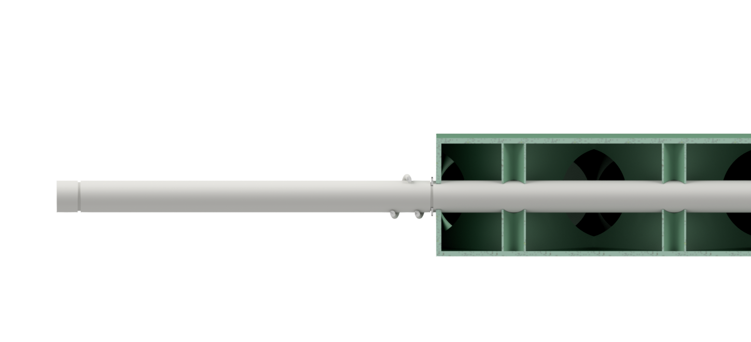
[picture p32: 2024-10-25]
Skripsie/Pictures/Rotor_AssemblyM2.png

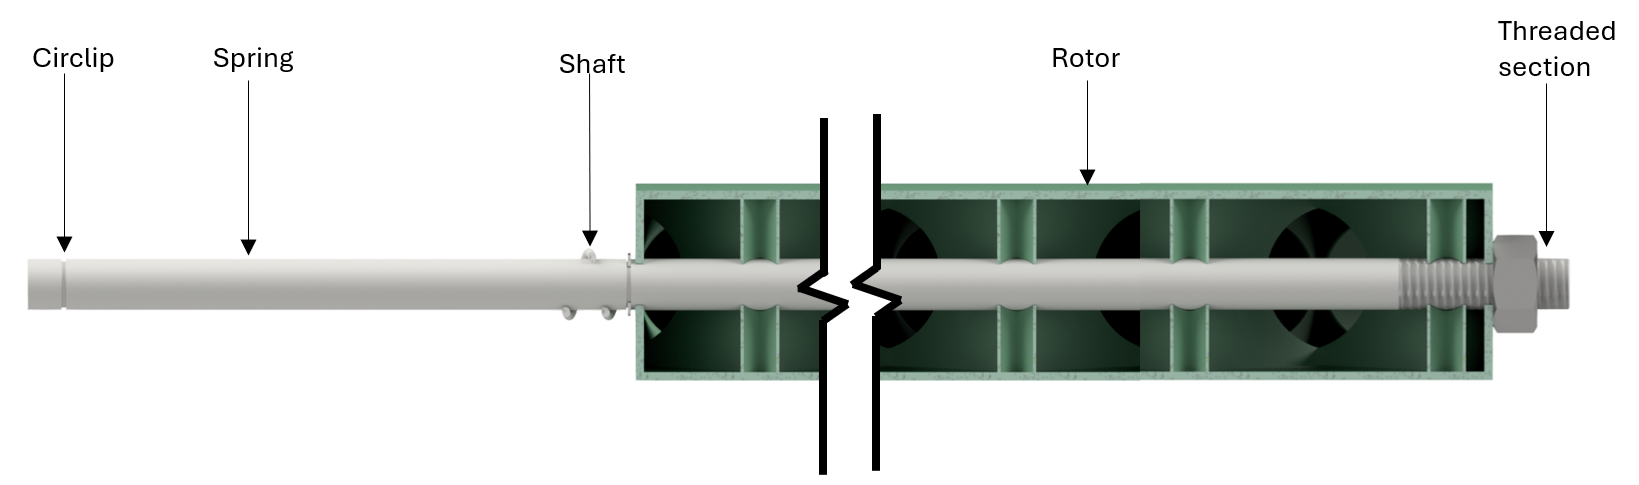
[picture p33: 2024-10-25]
Skripsie/Pictures/Rotor_AssemblyM2 Labled.png

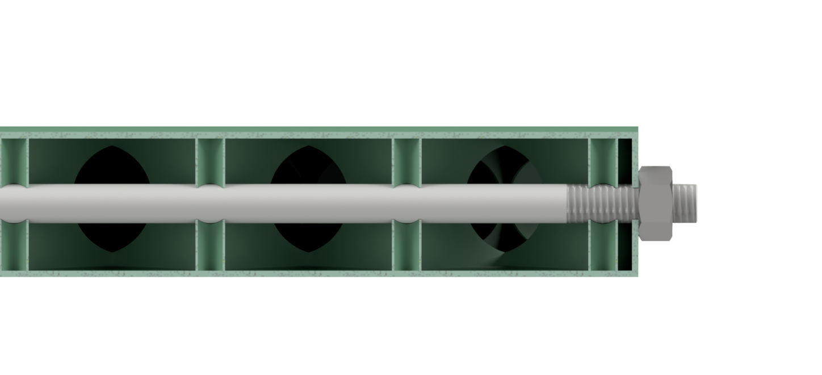
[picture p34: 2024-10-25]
Skripsie/Pictures/Rotor_AssemblyM2_End.png

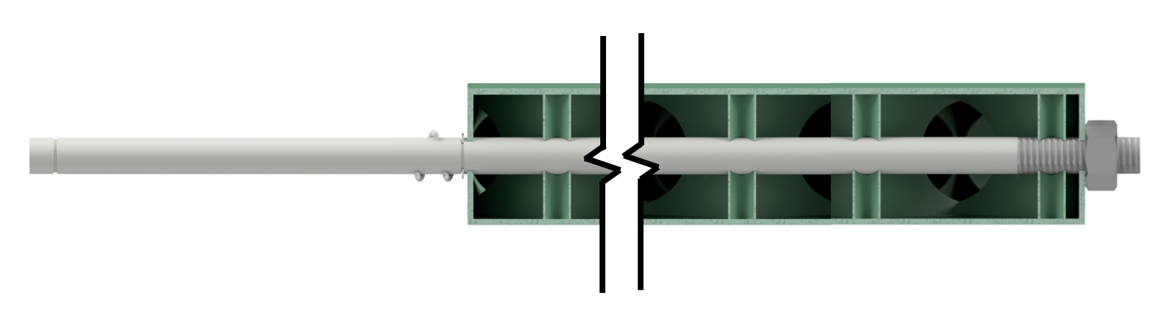
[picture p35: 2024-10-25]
Skripsie/Pictures/Rotor_AssemblyM2Unlabled.png

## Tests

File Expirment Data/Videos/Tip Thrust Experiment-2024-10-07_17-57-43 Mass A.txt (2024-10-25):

	mass A	
t	θ	
0.033	-11.5
0.067	-12.5
0.100	-12.5
0.133	-12.4
0.167	-12.4
0.200	-14.0
0.233	-17.6
0.267	-21.4
0.300	-25.0
0.333	-30.4
0.367	-35.5
0.400	-39.4
0.433	-44.2
0.467	-45.1
0.500	-45.9
0.533	-45.5
0.567	-44.6
0.600	-43.6
0.633	-42.4
0.667	-42.3
0.700	-42.3
0.733	-42.3
0.767	-42.5
0.800	-42.4
0.833	-42.7
0.867	-43.1
0.900	-43.0
0.933	-42.9
0.967	-42.9
1.000	-43.0
1.033	-43.0
1.067	-43.4
1.100	-43.5
1.133	-43.5
1.167	-43.7
1.200	-44.0
1.233	-44.1
1.267	-44.2
1.300	-44.4
1.333	-44.5
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

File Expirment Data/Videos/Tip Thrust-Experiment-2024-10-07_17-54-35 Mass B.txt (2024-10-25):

	mass B	
t	θ	
0.000	-6.4
0.033	-8.0
0.067	-40.2
0.100	-44.7
0.133	-50.1
0.167	-46.6
0.200	-48.8
0.233	-47.8
0.267	-45.4
0.300	-44.6
0.333	-42.3
0.367	-40.6
0.400	-41.1
0.433	-42.0
0.467	-40.2
0.500	-41.8
0.533	-41.2
0.567	-41.2
0.600	-38.5
0.633	-39.6
0.667	-38.8
0.700	-38.6
0.733	-38.2
0.767	-37.6
0.800	-36.9
0.833	-37.3
0.867	-37.2
0.900	-36.4
0.933	-35.6
0.967	-34.4
1.000	-33.1
1.033	-31.4
1.067	-29.5
1.100	-27.5
1.133	-25.1
1.167	-22.6
1.200	-19.4
1.233	-16.0
1.267	-12.9
1.300	-9.2
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

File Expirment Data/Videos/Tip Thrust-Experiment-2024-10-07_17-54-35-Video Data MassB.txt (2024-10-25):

	mass B	
t	θ	
0.100	-42.2
0.133	-46.2
0.167	-48.1
0.200	-48.4
0.233	-47.3
0.267	-44.3
0.300	-43.1
0.333	-42.2
0.367	-41.1
0.400	-40.7
0.433	-40.5
0.467	-40.6
0.500	-40.2
0.533	-40.4
0.567	-40.7
0.600	-40.1
0.633	-40.0
0.667	-39.6
0.700	-38.4
0.733	-38.0
0.767	-37.3
0.800	-36.6
0.833	-37.0
0.867	-36.7
0.900	-36.2
0.933	-35.2
0.967	-34.1
1.000	-33.0
1.033	-31.1
1.067	-29.3
1.100	-27.3
1.133	-24.9
1.167	-22.4
1.200	-19.4
1.233	-16.4
1.267	-12.6
1.300	-8.8
1.333	-4.9
1.367	-0.6
1.400	3.4
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

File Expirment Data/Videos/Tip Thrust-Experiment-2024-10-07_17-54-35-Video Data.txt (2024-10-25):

	mass A	
t	θ	
0.100	162.6
0.133	153.0
0.167	146.7
0.200	141.2
0.233	138.1
0.267	136.0
0.300	134.7
0.333	132.8
0.367	132.3
0.400	130.7
0.433	136.7
0.467	132.5
0.500	135.7
0.533	133.3
0.567	138.9
0.600	140.2
0.633	142.2
0.667	142.7
0.700	145.0
0.733	146.5
0.767	147.6
0.800	146.6
0.833	148.9
0.867	150.3
0.900	151.2
0.933	154.0
0.967	157.4
1.000	159.8
1.033	161.7
1.067	160.4
1.100	166.1
1.133	168.4
1.167	170.9
1.200	173.1
1.233	176.1
1.267	180.0
1.300	183.8
1.333	188.5
1.367	192.3
1.400	189.1
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

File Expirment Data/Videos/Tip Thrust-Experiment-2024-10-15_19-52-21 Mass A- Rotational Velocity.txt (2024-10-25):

	mass A	
t	ω	
0.067	
0.100	-57.9
0.133	-73.5
0.167	-89.0
0.200	-96.6
0.233	-107.2
0.267	-129.4
0.300	-146.0
0.333	-155.0
0.367	-168.3
0.400	-186.2
0.433	-193.0
0.467	-202.7
0.500	-225.9
0.533	-239.8
0.567	-246.8
0.600	-261.2
0.633	-293.7
0.667	-297.6
0.700	-299.7
0.733	-319.9
0.767	-332.9
0.800	-350.4
0.833	-402.8
0.867	-423.2
0.900	-429.5
0.933	-470.1
0.967	-474.4
1.000	-475.9
1.033	-432.5
1.067	-521.2
1.100	-584.5
1.133	-492.2
1.167	-450.8
1.200	-461.9
1.233	-597.7
1.267	-534.6
1.300	-456.6
1.333	-539.3
1.367	-523.6
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

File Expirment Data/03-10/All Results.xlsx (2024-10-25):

Target Pitch | P_1_i_0_d_0 | P_1_i_0.7_d_0 | P_1_i_1_d_0 | P_1_i_0.7_d_0.005
0 | -5 | -2 | 0 | 1
0 | -5 | -2 | 0 | 1
0 | -5 | -2 | 0 | 1
0 | -4 | -2 | 0 | 0
0 | -5 | -2 | 0 | 0
0 | -4 | -2 | 0 | 0
0 | -5 | -2 | 0 | 1
0 | -4 | -2 | 0 | 1
0 | -4 | -2 | 0 | 1
0 | -5 | -2 | 0 | 1
10 | -5 | -1 | 0 | 1
10 | -4 | -1 | 1 | 0
10 | -4 | -1 | 19 | -4
10 | 0 | 6 | 24 | -59
10 | 36 | 21 | 10 | -84
10 | 51 | 24 | 13 | -91
10 | 57 | 23 | 50 | -94
10 | 59 | 23 | 19 | -96
10 | 61 | 22 | 27 | -97
10 | 61 | 23 | 89 | -96
10 | 60 | 23 | 17 | -97
10 | 61 | 23 |  | -97
10 | 63 | 24 |  | -96
10 | 61 | 22 |  | -96
10 | 61 | 22 |  | -96
10 | 61 | 23 |  | -97
10 | 61 | 23 |  | -97
10 | 62 | 23 |  | -97
10 | 60 | 22 |  | -97
10 | 60 | 23 |  | -96
20 | 60 | 23 |  | -97
20 | 60 | 23 |  | -97
20 | 60 | 26 |  | -97
20 | 60 | 28 |  | -95
20 | 60 | 30 |  | -54
20 | 60 | 31 |  | 52
20 | 62 | 30 |  | 88
20 | 61 | 30 |  | 78
20 | 61 | 31 |  | 51
20 | 60 | 30 |  | 36
20 | 61 | 30 |  | 31
20 | 60 | 30 |  | 29
20 | 61 | 29 |  | 27
20 | 60 | 30 |  | 27
20 | 61 | 30 |  | 27
20 | 62 | 30 |  | 27
20 | 61 | 29 |  | 27
20 | 61 | 30 |  | 27
20 | 60 | 30 |  | 27
20 | 59 | 31 |  | 27
30 | 61 | 30 |  | 27
30 | 61 | 30 |  | 27
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

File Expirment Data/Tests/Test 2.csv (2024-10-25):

Timestamp | Target Speed | Current Speed | Target Pitch | Current Pitch 1 | Current Pitch 2 | Load Cell 1 | Load Cell 2 | Load Cell 3 | Load Cell 4
10/12/2024 16:35 | 0.01 | 0 | 0 | 494 | 548 | 4 | -5 | 25 | -38
10/12/2024 16:35 | 0.01 | 0 | 0 | 494 | 548 | 3 | -5 | 25 | -38
10/12/2024 16:35 | 0.01 | 0 | 0 | 494 | 548 | 4 | -6 | 26 | -39
10/12/2024 16:35 | 0.01 | 0 | 0 | 494 | 548 | 4 | -6 | 26 | -39
10/12/2024 16:35 | 0.01 | 0 | 0 | 494 | 548 | 4 | -5 | 26 | -39
10/12/2024 16:35 | 0.01 | 0 | 0 | 494 | 548 | 4 | -6 | 26 | -39
10/12/2024 16:35 | 0.01 | 0 | 0 | 494 | 548 | 4 | -5 | 25 | -39
10/12/2024 16:35 | 0.01 | 0 | 0 | 494 | 549 | 3 | -5 | 25 | -38
10/12/2024 16:35 | 0.01 | 0 | 0 | 494 | 549 | 3 | 10 | 35 | -43
10/12/2024 16:35 | 0.01 | 0 | 0 | 494 | 549 | 6 | -17 | 96 | -43
10/12/2024 16:35 | 0.01 | 0 | 0 | 494 | 549 | 44 | -240 | 270 | 389
10/12/2024 16:35 | 0.01 | 0 | 0 | 494 | 549 | 90 | -283 | 265 | 382
10/12/2024 16:35 | 0.01 | 0 | 0 | 494 | 549 | 74 | -282 | 279 | 375
10/12/2024 16:35 | 0.01 | 0 | 0 | 494 | 549 | 91 | -261 | 296 | 375
10/12/2024 16:35 | 0.01 | 0 | 0 | 494 | 548 | 97 | -294 | 279 | 436
10/12/2024 16:35 | 0.01 | 0 | 0 | 494 | 548 | 93 | -265 | 296 | 439
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

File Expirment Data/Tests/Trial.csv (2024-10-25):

Timestamp | Target Speed | Current Speed | Target Pitch | Current Pitch 1 | Current Pitch 2 | Load Cell 1 | Load Cell 2 | Load Cell 3 | Load Cell 4
2024-10-12 16:55:14 | 0.01 | 0.0 | 0.0 | 488.0 | 539.0 | 6.0 | 10.0 | -422.0 | -30.0
2024-10-12 16:55:14 | 0.01 | 0.0 | 0.0 | 488.0 | 539.0 | 6.0 | 9.0 | -422.0 | -30.0
2024-10-12 16:55:14 | 0.01 | 0.0 | 0.0 | 488.0 | 539.0 | 6.0 | 9.0 | -422.0 | -30.0
2024-10-12 16:55:14 | 0.01 | 0.0 | 0.0 | 488.0 | 539.0 | 7.0 | 9.0 | -422.0 | -30.0
2024-10-12 16:55:14 | 0.01 | 0.0 | 0.0 | 488.0 | 539.0 | 7.0 | 9.0 | -422.0 | -30.0
2024-10-12 16:55:14 | 0.01 | 0.0 | 0.0 | 488.0 | 539.0 | 7.0 | 9.0 | -422.0 | -31.0
2024-10-12 16:55:14 | 0.01 | 0.0 | 0.0 | 488.0 | 539.0 | 7.0 | 9.0 | -422.0 | -31.0
2024-10-12 16:55:14 | 0.01 | 0.0 | 0.0 | 488.0 | 539.0 | 7.0 | 9.0 | -422.0 | -30.0
2024-10-12 16:55:14 | 0.01 | 0.0 | 0.0 | 488.0 | 539.0 | 6.0 | 9.0 | -422.0 | -30.0
2024-10-12 16:55:14 | 0.01 | 0.0 | 0.0 | 488.0 | 539.0 | 6.0 | 10.0 | -422.0 | -52.0
2024-10-12 16:55:14 | 0.01 | 0.0 | 0.0 | 489.0 | 539.0 | 5.0 | 10.0 | -422.0 | 462.0
2024-10-12 16:55:14 | 0.01 | 0.0 | 0.0 | 489.0 | 539.0 | 185.0 | -448.0 | -422.0 | 853.0
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

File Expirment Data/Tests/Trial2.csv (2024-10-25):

Timestamp | Target Speed | Current Speed | Target Pitch | Current Pitch 1 | Current Pitch 2 | Load Cell 1 | Load Cell 2 | Load Cell 3 | Load Cell 4
2024-10-12 17:27:59 | 0.01 | 0.0 | 0.0 | 497.0 | 543.0 | 49.0 | -19.0 | 53.0 | -70.0
2024-10-12 17:27:59 | 0.01 | 0.0 | 0.0 | 497.0 | 543.0 | 48.0 | -19.0 | 52.0 | -70.0
2024-10-12 17:27:59 | 0.01 | 0.0 | 0.0 | 497.0 | 543.0 | 48.0 | -18.0 | 52.0 | -72.0
2024-10-12 17:27:59 | 0.01 | 0.0 | 0.0 | 497.0 | 543.0 | 49.0 | -2.0 | 57.0 | -68.0
2024-10-12 17:27:59 | 0.01 | 0.0 | 0.0 | 497.0 | 543.0 | 47.0 | -27.0 | 188.0 | -68.0
2024-10-12 17:27:59 | 0.01 | 0.0 | 0.0 | 497.0 | 543.0 | 33.0 | -592.0 | 622.0 | 1247.0
2024-10-12 17:27:59 | 0.01 | 0.0 | 0.0 | 497.0 | 543.0 | -80.0 | -502.0 | 677.0 | 1005.0
2024-10-12 17:27:59 | 0.01 | 0.0 | 0.0 | 497.0 | 543.0 | -4.0 | -365.0 | 677.0 | 1588.0
2024-10-12 17:27:59 | 0.01 | 0.0 | 0.0 | 497.0 | 543.0 | -47.0 | -539.0 | 796.0 | 1164.0
2024-10-12 17:27:59 | 0.01 | 0.0 | 0.0 | 497.0 | 543.0 | 81.0 | -326.0 | 600.0 | 978.0
2024-10-12 17:27:59 | 0.01 | 0.0 | 0.0 | 497.0 | 543.0 | 81.0 | -274.0 | 523.0 | 978.0
2024-10-12 17:27:59 | 0.01 | 0.0 | 0.0 | 497.0 | 543.0 | 133.0 | -163.0 | 424.0 | 697.0
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

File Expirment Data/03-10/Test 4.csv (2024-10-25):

Timestamp | Target Speed | Current Speed | Target Pitch | Current Pitch 1 | Current Pitch 2 | Load Cell 1 | Load Cell 2 | Load Cell 3 | Load Cell 4
2024-10-12 17:18:35 | 0.01 | 0.0 | 0.0 | 498.0 | 552.0 | 40.0 | -31.0 | 86.0 | -43.0
2024-10-12 17:18:35 | 0.01 | 0.0 | 0.0 | 498.0 | 552.0 | 40.0 | -32.0 | 86.0 | -43.0
2024-10-12 17:18:35 | 0.01 | 0.0 | 0.0 | 499.0 | 552.0 | 40.0 | -32.0 | 86.0 | -43.0
2024-10-12 17:18:35 | 0.01 | 0.0 | 0.0 | 499.0 | 552.0 | 40.0 | -32.0 | 86.0 | -43.0
2024-10-12 17:18:35 | 0.01 | 0.0 | 0.0 | 499.0 | 552.0 | 40.0 | -31.0 | 86.0 | -42.0
2024-10-12 17:18:35 | 0.01 | 0.0 | 0.0 | 499.0 | 552.0 | 40.0 | -32.0 | 86.0 | -42.0
2024-10-12 17:18:35 | 0.01 | 0.0 | 0.0 | 499.0 | 552.0 | 41.0 | -12.0 | 91.0 | -37.0
2024-10-12 17:18:35 | 0.01 | 0.0 | 0.0 | 499.0 | 552.0 | 31.0 | -98.0 | 275.0 | -37.0
2024-10-12 17:18:35 | 0.01 | 0.0 | 0.0 | 498.0 | 552.0 | -135.0 | -330.0 | 469.0 | 521.0
2024-10-12 17:18:35 | 0.01 | 0.0 | 0.0 | 498.0 | 552.0 | -170.0 | -379.0 | 502.0 | 541.0
2024-10-12 17:18:35 | 0.01 | 0.0 | 0.0 | 498.0 | 552.0 | -172.0 | -382.0 | 506.0 | 537.0
2024-10-12 17:18:35 | 0.01 | 0.0 | 0.0 | 498.0 | 552.0 | -173.0 | -377.0 | 506.0 | 537.0
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

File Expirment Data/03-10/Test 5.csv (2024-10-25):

Timestamp | Target Speed | Current Speed | Target Pitch | Current Pitch 1 | Current Pitch 2 | Load Cell 1 | Load Cell 2 | Load Cell 3 | Load Cell 4
2024-10-12 17:26:09 | 0.01 | 0.0 | 0.0 | 481.0 | 546.0 | 51.0 | -25.0 | 56.0 | -74.0
2024-10-12 17:26:09 | 0.01 | 0.0 | 0.0 | 481.0 | 546.0 | 52.0 | -24.0 | 55.0 | -74.0
2024-10-12 17:26:09 | 0.01 | 0.0 | 0.0 | 481.0 | 546.0 | 52.0 | -25.0 | 55.0 | -74.0
2024-10-12 17:26:09 | 0.01 | 0.0 | 0.0 | 481.0 | 545.0 | 52.0 | -25.0 | 55.0 | -74.0
2024-10-12 17:26:09 | 0.01 | 0.0 | 0.0 | 481.0 | 545.0 | 52.0 | -25.0 | 55.0 | -74.0
2024-10-12 17:26:09 | 0.01 | 0.0 | 0.0 | 481.0 | 545.0 | 51.0 | -24.0 | 55.0 | -74.0
2024-10-12 17:26:09 | 0.01 | 0.0 | 0.0 | 481.0 | 545.0 | 51.0 | -24.0 | 138.0 | 332.0
2024-10-12 17:26:09 | 0.01 | 0.0 | 0.0 | 481.0 | 545.0 | -68.0 | -366.0 | 138.0 | 332.0
2024-10-12 17:26:09 | 0.01 | 0.0 | 0.0 | 481.0 | 545.0 | -136.0 | -366.0 | 508.0 | 661.0
2024-10-12 17:26:09 | 0.01 | 0.0 | 0.0 | 481.0 | 545.0 | -81.0 | -389.0 | 475.0 | 638.0
2024-10-12 17:26:09 | 0.01 | 0.0 | 0.0 | 481.0 | 545.0 | -97.0 | -400.0 | 495.0 | 638.0
2024-10-12 17:26:09 | 0.01 | 0.0 | 0.0 | 481.0 | 545.0 | -119.0 | -385.0 | 494.0 | 641.0
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

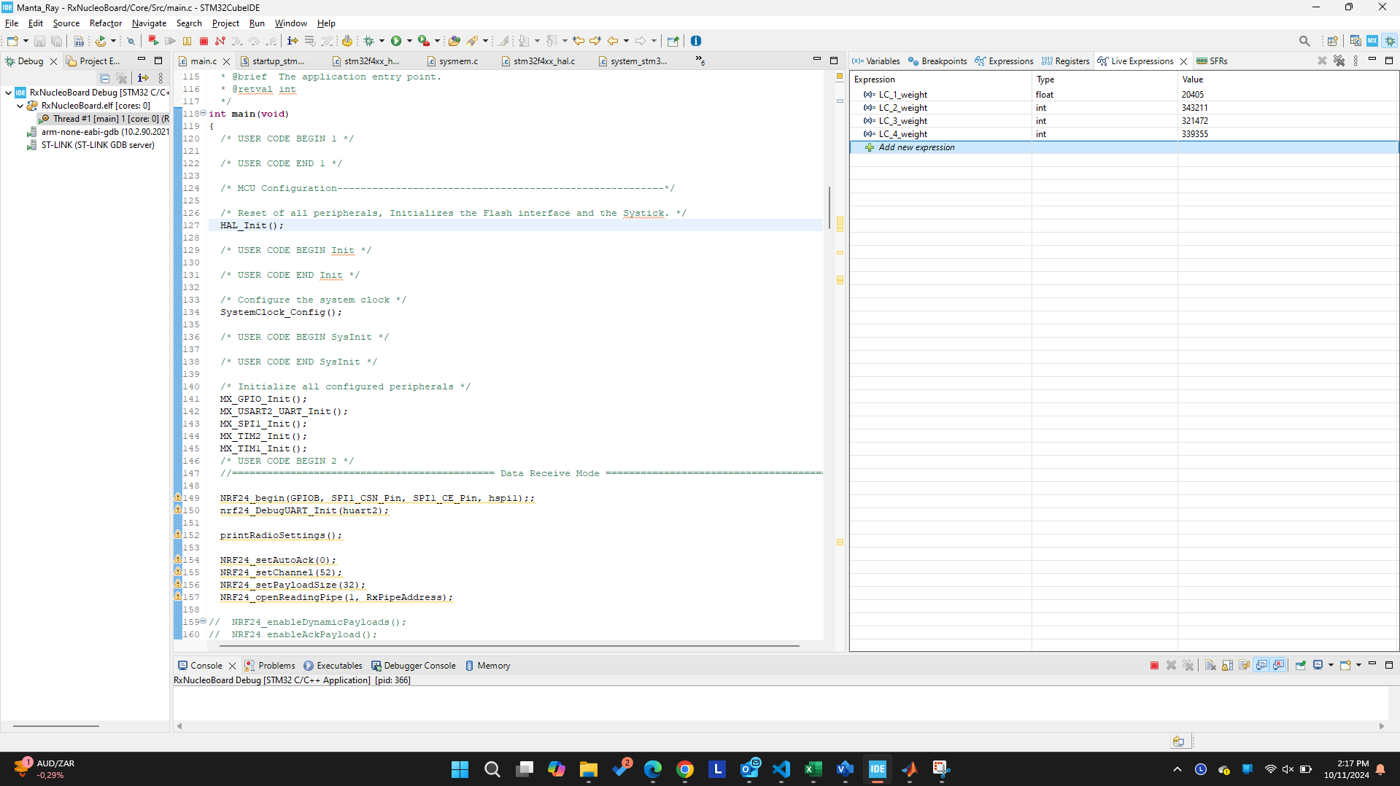
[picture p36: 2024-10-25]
Skripsie/Pictures/Calibration 1.png

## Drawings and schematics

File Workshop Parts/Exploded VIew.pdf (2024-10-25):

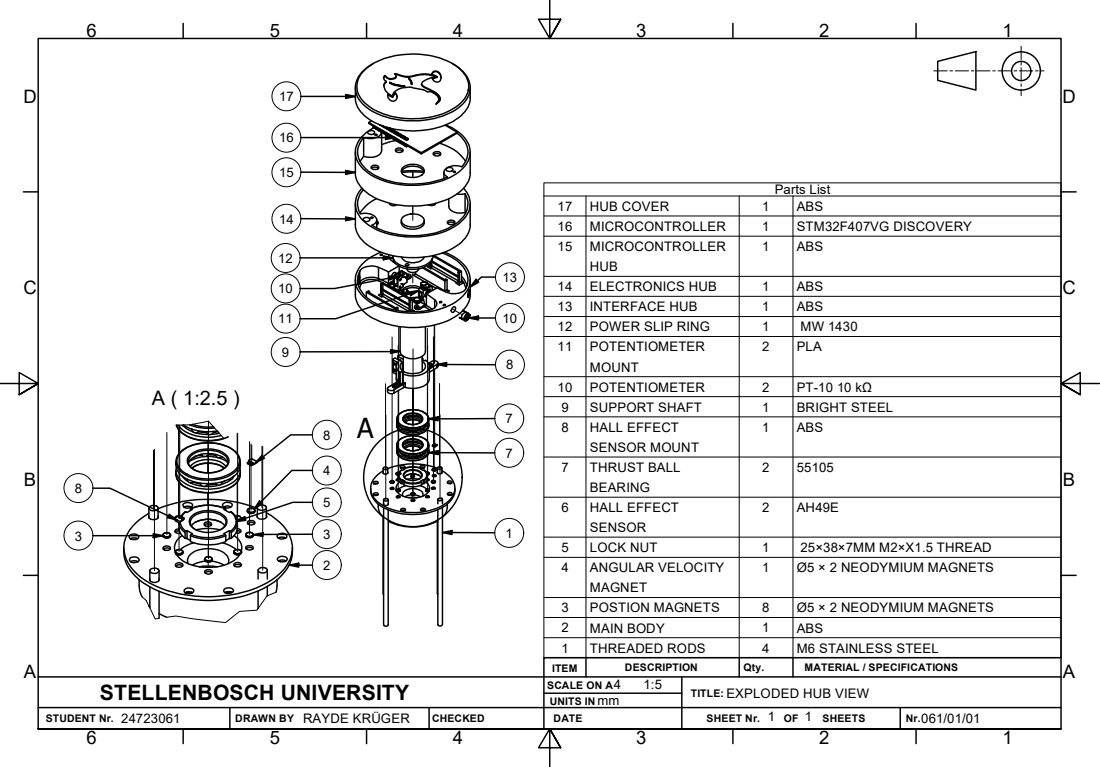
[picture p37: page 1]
Parts List; STUDENT Nr.; DRAWN BY; CHECKED; UNITS IN; SHEET Nr.; SHEETS; RAYDE KRÜGER

17 | HUB COVER | 1 | ABS
16 | MICROCONTROLLER | 1 | STM32F407VG DISCOVERY
15 | MICROCONTROLLER HUB | 1 | ABS

14 | ELECTRONICS HUB | 1 | ABS
13 | INTERFACE HUB | 1 | ABS
12 | POWER SLIP RING | 1 | MW 1430
11 | POTENTIOMETER MOUNT | 2 | PLA

10 | POTENTIOMETER | 2 | PT-10 10 kΩ
9 | SUPPORT SHAFT | 1 | BRIGHT STEEL
8 | HALL EFFECT SENSOR MOUNT | 1 | ABS

7 | THRUST BALL BEARING | 2 | 55105

6 | HALL EFFECT SENSOR | 2 | AH49E

5 | LOCK NUT | 1 | 25×38×7MM M2×X1.5 THREAD
4 | ANGULAR VELOCITY MAGNET | 1 | Ø5 × 2 NEODYMIUM MAGNETS

3 | POSTION MAGNETS | 8 | Ø5 × 2 NEODYMIUM MAGNETS
2 | MAIN BODY | 1 | ABS
1 | THREADED RODS | 4 | M6 STAINLESS STEEL

ITEM | DESCRIPTION | Qty. | MATERIAL / SPECIFICATIONS

STELLENBOSCH UNIVERSITY | SCALE ON A 4 1:5 | TITLE: EXPLODED HUB VIEW

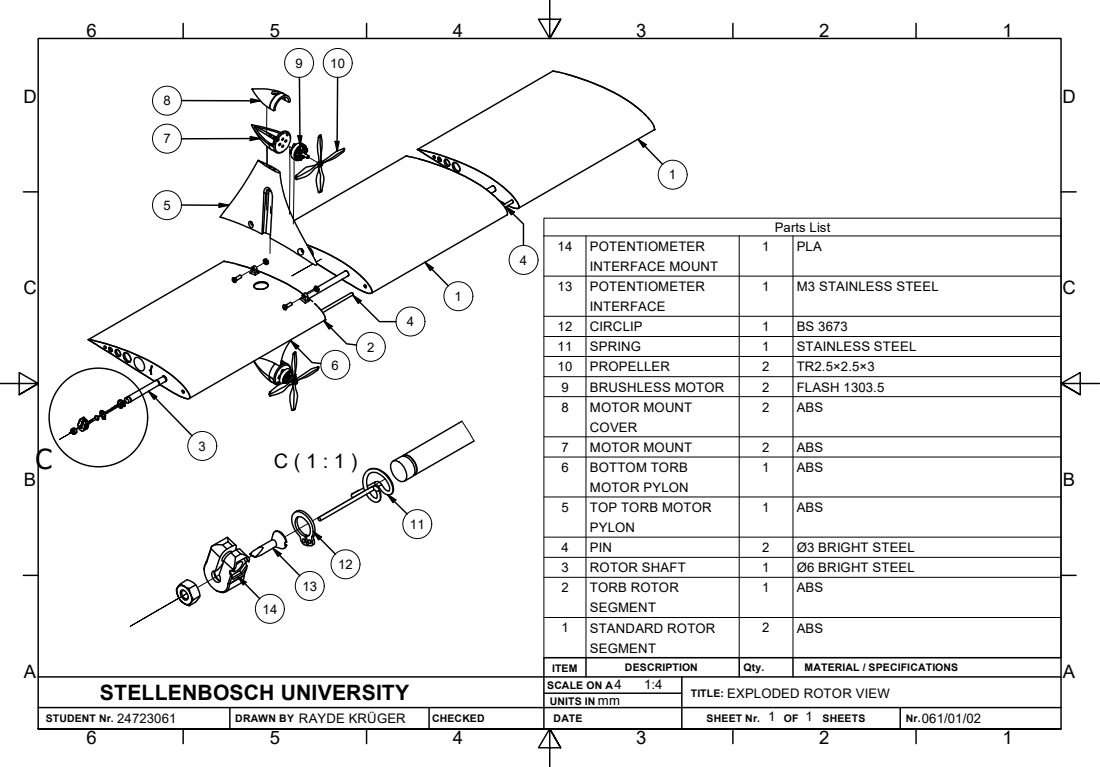
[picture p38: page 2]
Parts List; STUDENT Nr.; DRAWN BY; CHECKED; UNITS IN; SHEET Nr.; SHEETS; RAYDE KRÜGER

14 | POTENTIOMETER INTERFACE MOUNT | 1 | PLA

13 | POTENTIOMETER INTERFACE | 1 | M3 STAINLESS STEEL

12 | CIRCLIP | 1 | BS 3673
11 | SPRING | 1 | STAINLESS STEEL
10 | PROPELLER | 2 | TR2.5×2.5×3
9 | BRUSHLESS MOTOR | 2 | FLASH 1303.5
8 | MOTOR MOUNT COVER | 2 | ABS

7 | MOTOR MOUNT | 2 | ABS
6 | BOTTOM TORB MOTOR PYLON | 1 | ABS

5 | TOP TORB MOTOR PYLON | 1 | ABS

4 | PIN | 2 | Ø3 BRIGHT STEEL
3 | ROTOR SHAFT | 1 | Ø6 BRIGHT STEEL
2 | TORB ROTOR SEGMENT | 1 | ABS

1 | STANDARD ROTOR SEGMENT | 2 | ABS

ITEM | DESCRIPTION | Qty. | MATERIAL / SPECIFICATIONS

STELLENBOSCH UNIVERSITY | 4 1:4 SCALE ON A | TITLE: EXPLODED ROTOR VIEW

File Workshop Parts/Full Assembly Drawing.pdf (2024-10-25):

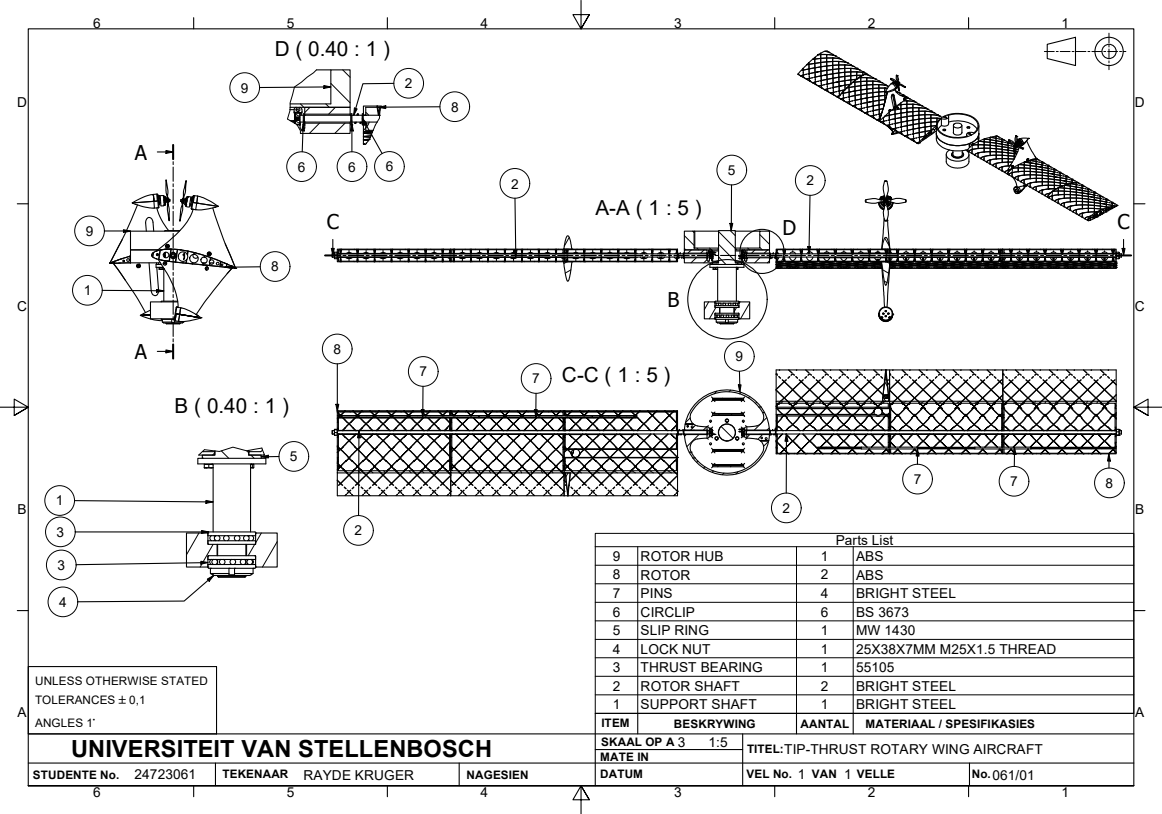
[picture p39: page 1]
Parts List; ROTOR HUB; ABS; PINS; BRIGHT STEEL; CIRCLIP; SLIP RING; LOCK NUT; 25X38X7MM M25X1.5 THREAD; THRUST BEARING; ROTOR SHAFT; SUPPORT SHAFT; STUDENTE No.; TEKENAAR; NAGESIEN; ITEM; BESKRYWING; AANTAL; MATERIAAL / SPESIFIKASIES; SKAAL OP A MATE IN; VEL No.; VAN; VELLE; RAYDE KRUGER

UNLESS OTHERWISE STATED
TOLERANCES `0,1
ANGLES 1~
UNIVERSITEIT VAN STELLENBOSCH

TIP-THRUST ROTARY WING AIRCRAFT

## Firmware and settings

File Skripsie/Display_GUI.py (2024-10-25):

import sys
import serial
import time
import threading
import csv
from PyQt5.QtWidgets import QApplication, QWidget, QVBoxLayout, QHBoxLayout, QPushButton, QLabel, QTextEdit, QGridLayout, QFileDialog
from PyQt5.QtGui import QFont 
from PyQt5.QtCore import QTimer, pyqtSignal, QObject
import pyqtgraph as pg
from datetime import datetime

# Signal class to safely send data from thread to GUI
class SerialListener(QObject):
    data_received = pyqtSignal(str)

# Serial setup (modify 'COM4' to your port)
try:
    ser = serial.Serial('COM4', 115200, timeout=1)
    print("Connected to COM4 at 115200 baud rate")
except serial.SerialException as e:
    print(f"Error opening serial port: {e}")
    ser = None

# Function to listen for incoming data
def listen_for_data(serial_listener):
    if ser:
        while True:
            try:
                if ser.in_waiting > 0:
                    received_data = ser.readline().decode('utf-8').strip()
                    print(f"DEBUG: Raw data received -> {received_data}")
                    if received_data:
                        serial_listener.data_received.emit(received_data)
            except serial.SerialException as e:
                print(f"Error reading from serial port: {e}")
                break

class DroneControlGUI(QWidget):
    def __init__(self):
        super().__init__()
        self.initUI()

        # Serial listener
        self.serial_listener = SerialListener()
        self.serial_listener.data_received.connect(self.handle_cdc_data)

        # Timer to update the graphs every second
        self.graph_update_timer = QTimer()
        self.graph_update_timer.timeout.connect(self.update_graphs)
        self.graph_update_timer.start(50)

        # Initialize data arrays
        self.target_speed_data = []
        self.current_speed_data = []
        self.target_pitch_data = []
        self.current_pitch_1_data = []
        self.current_pitch_2_data = []
        self.loadcell_data = [[] for _ in range(4)]  # Four load cell data arrays
        self.timestamps = []  # To track timestamps

        # Track the last known values
        self.last_speed = 0.0
        self.last_pitch_1 = 0.0
        self.last_pitch_2 = 0.0
        self.last_weights = [0.0] * 4

    def initUI(self):
        # Window settings
        self.setWindowTitle('Drone Control GUI')
        self.setGeometry(100, 100, 1000, 800)

        # CDC log area
        self.cdc_log = QTextEdit(self)
        self.cdc_log.setReadOnly(True)
        self.cdc_log.setFont(QFont('Arial', 10))

        # Labels for speed and pitch
        self.current_speed_label = QLabel('Current Speed: 0')
        self.current_pitch_label = QLabel('Current Pitch 1: 0, Pitch 2: 0')
        self.target_speed_label = QLabel('Target Speed: 0')
        self.target_pitch_label = QLabel('Target Pitch: 0')

        # Graphs for Speed, Pitch, and Load Cells
        self.speed_graph = pg.PlotWidget(self)
        self.speed_graph.setTitle('Speed Graph')
        self.speed_graph.addLegend()

        self.pitch_graph = pg.PlotWidget(self)
        self.pitch_graph.setTitle('Pitch Graph')
        self.pitch_graph.addLegend()

        # Load cell graph
        self.loadcell_graph = pg.PlotWidget(self)
        self.loadcell_graph.setTitle('Load Cell Graph')
        self.loadcell_graph.addLegend()

        # Speed and pitch curves
        self.speed_target_curve = self.speed_graph.plot(pen='g', name="Target Speed")
        self.speed_current_curve = self.speed_graph.plot(pen='r', name="Current Speed")

        self.pitch_target_curve = self.pitch_graph.plot(pen='g', name="Target Pitch")
        self.pitch_current_1_curve = self.pitch_graph.plot(pen='r', name="Current Pitch 1")
        self.pitch_current_2_curve = self.pitch_graph.plot(pen='b', name="Current Pitch 2")

        # Load cell curves
        self.loadcell_curves = [self.loadcell_graph.plot(pen=pg.intColor(i), name=f"Load Cell {i+1}") for i in range(4)]

        # Save to CSV button
        self.save_csv_button = QPushButton('Save to CSV', self)
        self.save_csv_button.clicked.connect(self.save_to_csv)

        # Layout
        self.layoutUI()

    def layoutUI(self):
        grid = QGridLayout()

        # Control buttons
        grid.addWidget(self.current_speed_label, 0, 0)
        grid.addWidget(self.current_pitch_label, 0, 1)
        grid.addWidget(self.target_speed_label, 0, 2)
        grid.addWidget(self.target_pitch_label, 0, 3)
        grid.addWidget(self.save_csv_button, 0, 4)

        # Graphs for speed, pitch, and load cells
        grid.addWidget(self.speed_graph, 1, 0, 1, 5)
        grid.addWidget(self.pitch_graph, 2, 0, 1, 5)
        grid.addWidget(self.loadcell_graph, 3, 0, 1, 5)  # Load cell graph

        # CDC Log
        grid.addWidget(QLabel('CDC Log:'), 4, 0)
        grid.addWidget(self.cdc_log, 5, 0, 1, 5)

        self.setLayout(grid)

    def handle_cdc_data(self, message):
        self.cdc_log.append(f"Received: {message}")
        print(f"DEBUG: CDC Data received -> {message}")

        current_time = datetime.now().strftime('%Y-%m-%d %H:%M:%S')

        if message.startswith("&_DATA"):
            try:
                clean_message = message[7:-1]
                parts = clean_message.split('_')

                if len(parts) >= 5:
                    current_speed = float(parts[0])
                    target_speed= float(parts[1])
                    target_pitch = float(parts[2])
                    current_pitch_1 = float(parts[3])
                    current_pitch_2 = float(parts[4])

                    # Update the last known values
                    self.last_speed = current_speed
                    self.last_pitch_1 = current_pitch_1
                    self.last_pitch_2 = current_pitch_2

                    # Append the data and timestamps
                    self.target_speed_data.append(target_speed)
                    self.current_speed_data.append(current_speed)
                    self.target_pitch_data.append(target_pitch)
                    self.current_pitch_1_data.append(current_pitch_1)
                    self.current_pitch_2_data.append(current_pitch_2)
                    self.timestamps.append(current_time)

                    self.current_speed_label.setText(f'Current Speed: {current_speed:.2f}')
                    self.current_pitch_label.setText(f'Current Pitch 1: {current_pitch_1:.2f}, Pitch 2: {current_pitch_2:.2f}')
                    self.target_speed_label.setText(f'Target Speed: {target_speed:.2f}')
                    self.target_pitch_label.setText(f'Target Pitch: {target_pitch:.2f}')

                    print(f"DEBUG: Parsed Data -> Target Speed: {target_speed}, Current Speed: {current_speed}, "
                          f"Target Pitch: {target_pitch}, Current Pitch 1: {current_pitch_1}, Current Pitch 2: {current_pitch_2}")
                else:
                    print("ERROR: Insufficient data received")
            except (IndexError, ValueError) as e:
                print(f"Error parsing CDC data: {e}")

        elif message.startswith("&_WGT"):
            try:
                clean_message = message[6:-1]  # Remove '&_WGT_' prefix and '*' suffix
                # Split the message and convert to float, preserving negative signs
                parts = [float(x) for x in clean_message.split('_') if x]
                if len(parts) >= 4:
                    # Update load cell data and maintain last weights
                    for i in range(4):
                        if i < len(parts):
                            self.loadcell_data[i].append(parts[i])
                            self.last_weights[i] = parts[i]  # Update last known weight
                        else:
                            # Append the last known weight if no new data received
                            self.loadcell_data[i].append(self.last_weights[i])

                    print(f"DEBUG: Parsed Load Cell Data -> {self.loadcell_data[0][-1]}, {self.loadcell_data[1][-1]}, "
                          f"{self.loadcell_data[2][-1]}, {self.loadcell_data[3][-1]}")
                else:
                    print("ERROR: Insufficient load cell data received")
            except (IndexError, ValueError) as e:
                print(f"Error parsing Load Cell data: {e}")

    def update_graphs(self):
        self.speed_target_curve.setData(self.target_speed_data)
        self.speed_current_curve.setData(self.current_speed_data)

        self.pitch_target_curve.setData(self.target_pitch_data)
        self.pitch_current_1_curve.setData(self.current_pitch_1_data)
        self.pitch_current_2_curve.setData(self.current_pitch_2_data)

        for i in range(4):
            self.loadcell_curves[i].setData(self.loadcell_data[i])

    def save_to_csv(self):
        options = QFileDialog.Options()
        filename, _ = QFileDialog.getSaveFileName(self, "Save Data", "", "CSV Files (*.csv)", options=options)
        if filename:
            with open(filename, mode='w', newline='') as csv_file:
                writer = csv.writer(csv_file)
                # Write header
                writer.writerow(['Timestamp', 'Target Speed', 'Current Speed', 'Target Pitch', 'Current Pitch 1', 'Current Pitch 2', 
                                 'Load Cell 1', 'Load Cell 2', 'Load Cell 3', 'Load Cell 4'])
                # Write data rows
                for i in range(len(self.target_speed_data)):
                    # Use the timestamp corresponding to the current index
                    timestamp = self.timestamps[i] if i < len(self.timestamps) else ''
                    writer.writerow([
                        timestamp,
                        self.target_speed_data[i] if i < len(self.target_speed_data) else '',
                        self.current_speed_data[i] if i < len(self.current_speed_data) else '',
                        self.target_pitch_data[i] if i < len(self.target_pitch_data) else '',
                        self.current_pitch_1_data[i] if i < len(self.current_pitch_1_data) else '',
                        self.current_pitch_2_data[i] if i < len(self.current_pitch_2_data) else '',
                        self.loadcell_data[0][i] if i < len(self.loadcell_data[0]) else '',
                        self.loadcell_data[1][i] if i < len(self.loadcell_data[1]) else '',
                        self.loadcell_data[2][i] if i < len(self.loadcell_data[2]) else '',
                        self.loadcell_data[3][i] if i < len(self.loadcell_data[3]) else '',
                    ])
            print(f"Data saved to {filename}")

def main():
    app = QApplication(sys.argv)
    gui = DroneControlGUI()

    # Start the serial listener in a separate thread
    listener_thread = threading.Thread(target=listen_for_data, args=(gui.serial_listener,))
    listener_thread.daemon = True
    listener_thread.start()

    gui.show()
    sys.exit(app.exec_())

if __name__ == '__main__':
    main()

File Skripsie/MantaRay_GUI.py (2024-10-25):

import sys
import serial
import time
import threading
from PyQt5.QtWidgets import QApplication, QWidget, QVBoxLayout, QHBoxLayout, QPushButton, QLabel, QLineEdit, QTextEdit, QGridLayout, QSlider, QMessageBox
from PyQt5.QtGui import QFont
from PyQt5.QtCore import QTimer, pyqtSignal, QObject, Qt
import pyqtgraph as pg
import os
import csv
from datetime import datetime

# Signal class to safely send data from thread to GUI
class SerialListener(QObject):
    data_received = pyqtSignal(str)

# Serial setup (modify 'COM4' to your port)
try:
    ser = serial.Serial('COM4', 115200, timeout=1)
    print("Connected to COM4 at 115200 baud rate")
except serial.SerialException as e:
    print(f"Error opening serial port: {e}")
    ser = None

# Function to listen for incoming data
def listen_for_data(serial_listener):
    if ser:
        while True:
            try:
                if ser.in_waiting > 0:
                    received_data = ser.readline().decode('utf-8').strip()
                    if received_data:
                        serial_listener.data_received.emit(received_data)
            except serial.SerialException as e:
                print(f"Error reading from serial port: {e}")
                break

class DataLoggerGUI(QWidget):
    def __init__(self):
        super().__init__()
        self.initUI()

        # Serial listener
        self.serial_listener = SerialListener()
        self.serial_listener.data_received.connect(self.handle_data)

        # Timer to update the graphs
        self.graph_update_timer = QTimer()
        self.graph_update_timer.timeout.connect(self.update_graphs)
        self.graph_update_timer.start(50)

        # Initialize data arrays
        self.data_array = []
        
    def initUI(self):
        # Window settings
        self.setWindowTitle('Data Logger GUI')
        self.setGeometry(100, 100, 1000, 800)

        # CDC log area
        self.cdc_log = QTextEdit(self)
        self.cdc_log.setReadOnly(True)
        self.cdc_log.setFont(QFont('Arial', 10))

        # Input and control buttons
        self.start_button = QPushButton('Start Logging', self)
        self.start_button.clicked.connect(self.start_logging)
        
        self.stop_button = QPushButton('Stop Logging', self)
        self.stop_button.clicked.connect(self.stop_logging)

        self.save_button = QPushButton('Save Data', self)
        self.save_button.clicked.connect(self.save_data)

        # Labels for received data
        self.data_label = QLabel('Received Data:')
        self.data_value_label = QLabel('No Data Received Yet')

        # Graph for received data
        self.data_graph = pg.PlotWidget(self)
        self.data_graph.setTitle('Data Graph')
        self.data_curve = self.data_graph.plot(pen='g', name='Data')

        # Layout
        self.layoutUI()

    def layoutUI(self):
        grid = QGridLayout()

        # Control buttons
        grid.addWidget(self.start_button, 0, 0)
        grid.addWidget(self.stop_button, 0, 1)
        grid.addWidget(self.save_button, 0, 2)

        # Data display
        grid.addWidget(self.data_label, 1, 0)
        grid.addWidget(self.data_value_label, 1, 1, 1, 2)

        # Graph for data
        grid.addWidget(self.data_graph, 2, 0, 1, 3)

        # CDC Log
        grid.addWidget(QLabel('CDC Log:'), 3, 0)
        grid.addWidget(self.cdc_log, 4, 0, 1, 3)

        self.setLayout(grid)

    def handle_data(self, message):
        self.cdc_log.append(f"Received: {message}")
        self.data_value_label.setText(f"Received: {message}")
        self.data_array.append(float(message))  # Assuming the message is a float

    def update_graphs(self):
        self.data_curve.setData(self.data_array)

    def start_logging(self):
        self.data_array.clear()  # Clear previous data
        self.cdc_log.append("Logging Started")

    def stop_logging(self):
        self.cdc_log.append("Logging Stopped")

    def save_data(self):
        if self.data_array:
            try:
                current_time = datetime.now().strftime('%Y-%m-%d_%H-%M-%S')
                file_name = f"Data_Logger_{current_time}.csv"
                file_path = os.path.join(os.getcwd(), file_name)

                # Write the data to a CSV file
                with open(file_path, mode='w', newline='') as file:
                    writer = csv.writer(file)
                    writer.writerow(['Data'])
                    for data in self.data_array:
                        writer.writerow([data])

                self.cdc_log.append(f"Data saved to {file_path}")
            except Exception as e:
                self.cdc_log.append(f"Error saving data: {e}")

if __name__ == '__main__':
    app = QApplication(sys.argv)
    ex = DataLoggerGUI()

    # Start the listener in a separate thread
    listener_thread = threading.Thread(target=listen_for_data, args=(ex.serial_listener,), daemon=True)
    listener_thread.start()

    ex.show()
    sys.exit(app.exec_())

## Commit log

2024-10-25 Full Project FIle which stores all the information the student used while doing the project
    [All Results.xlsx, Bottom Motor Mount.stp, Bottom_Pylon_200.stl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]
2024-10-25 Reformatted and added the Code
    [All Results.xlsx, Circlip Failure.csv, Decision_Matrix.xlsx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]
2024-11-16 Add files via upload
    PowerPoint Presentation
